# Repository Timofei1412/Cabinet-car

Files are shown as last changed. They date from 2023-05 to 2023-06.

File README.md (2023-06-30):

# Команда Кабинетный Болид
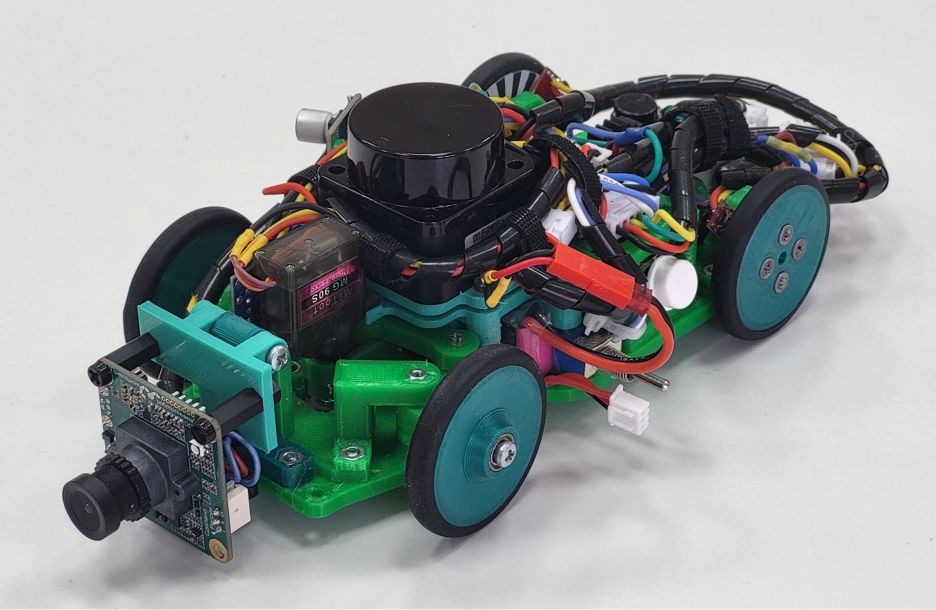
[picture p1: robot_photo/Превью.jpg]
General


### Робот, созданный для решения задачи РРО Будущие инженеры 2023
### © Беззубцев Федор, Федоров Тимофей 

## Наши фотографии
  [Обычная фотография](https://github.com/Timofei1412/Cabinet-car/blob/main/team_photo/Фотграфия%20команды.jpg)
  [Смешная фотография](https://github.com/Timofei1412/Cabinet-car/blob/main/team_photo/Смешная%20фотография.jpg)
<br>

## Видео заезда нашего робота на [Youtube](https://www.youtube.com/watch?v=HyZGGjBNKJ4&ab_channel=qZer0)
<br>

## Предисловие
  > Робот является автомобилем с передними поворотными колесами и задним приводом. На роботе установлены: лидар, для определения стенок и кубиков, на подпружиненной основе (для более удобной настройки уровня лидара), камерой для определения цвета кубиков и энкодер на ведущем двигателе, для определения пройденного расстояния. Система курсового управления автомобиля управляется сервомотором. При проектировании были учитаны углы Аккермана и принцип трапеции Жанто. Во главе робота находится микроконтроллер ESP32.
  
## Содержание репозитория
  - Папка "Robot models" содержит все модели старой версии робота
  - Папка "Code" содержит код робота
  - Папка "schematic" содержит электромеханическую схему робота
  - Папка "team_photo" содержит два фото команды по регламенту
  - Папка "robot_photo" содержит обзорные фото робота с шести сторон
  - Папка "readme_photo" содержит фото, используемые в README.md файле

## Фото робота
  Здесь представлены фото робота спереди, сзади, справа, слева, сверху и снизу.
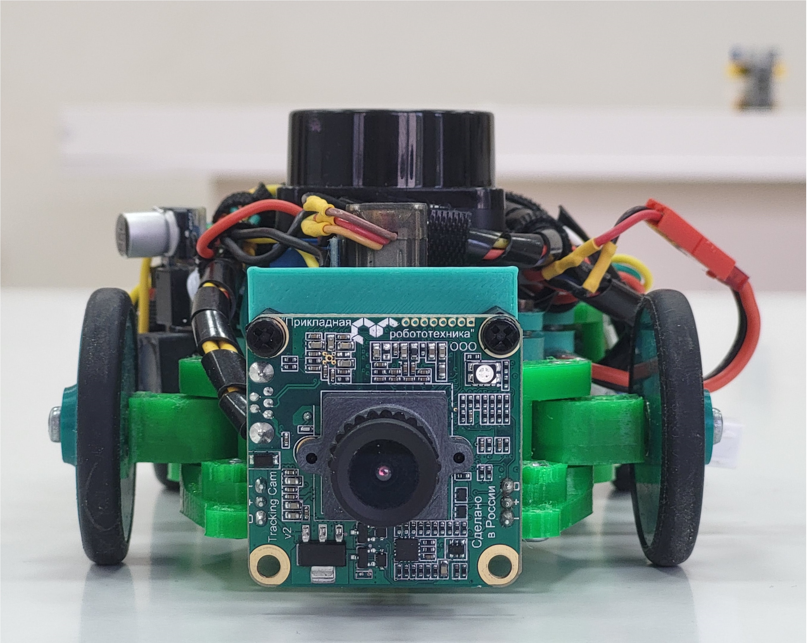
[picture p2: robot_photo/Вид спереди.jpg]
Front
  
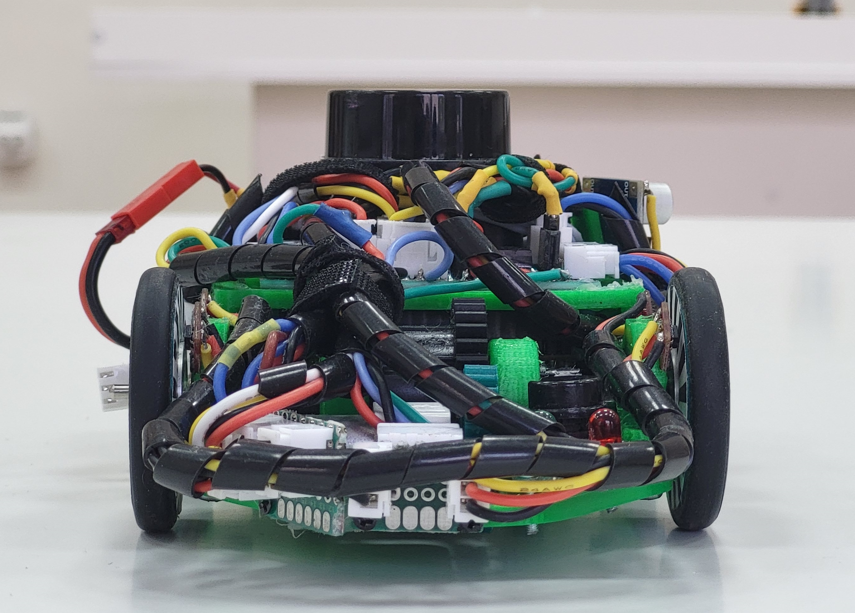
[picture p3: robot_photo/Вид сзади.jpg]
Back
  
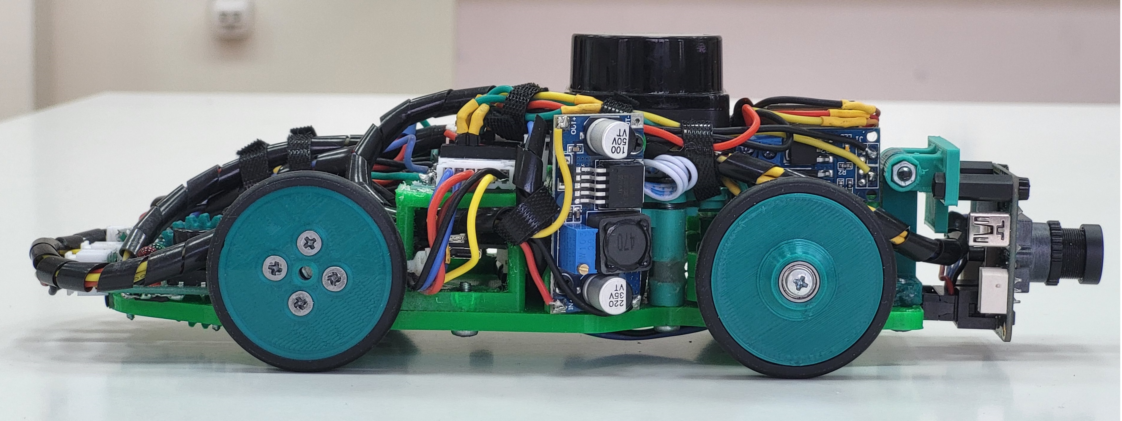
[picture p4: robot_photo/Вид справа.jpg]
Right
  
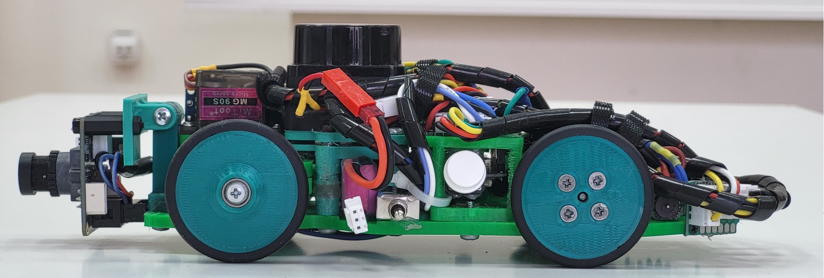
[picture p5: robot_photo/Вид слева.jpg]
Left
  
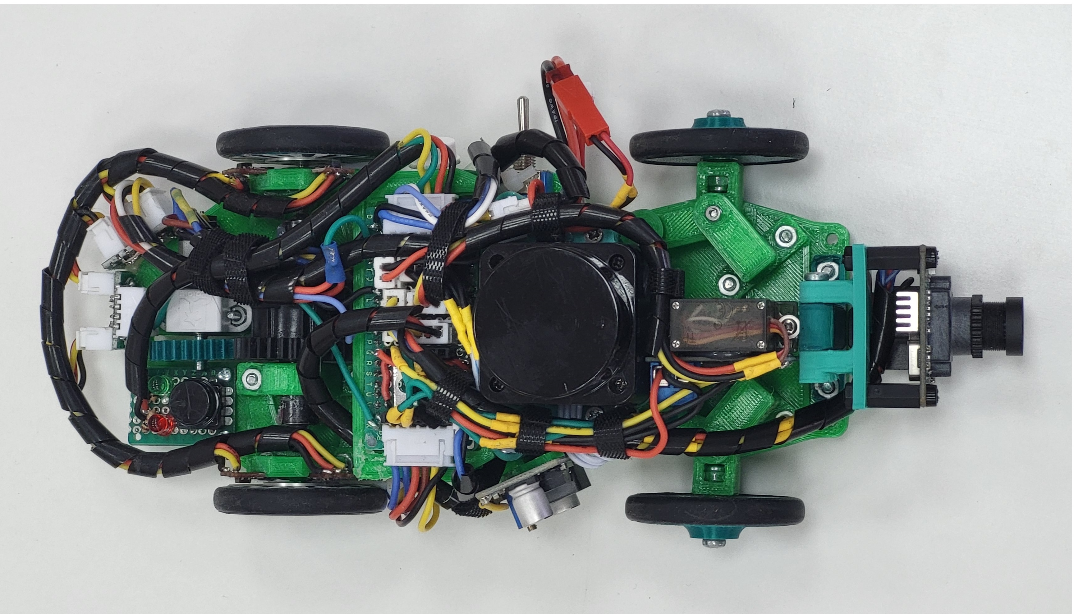
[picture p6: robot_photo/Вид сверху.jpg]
Top
  
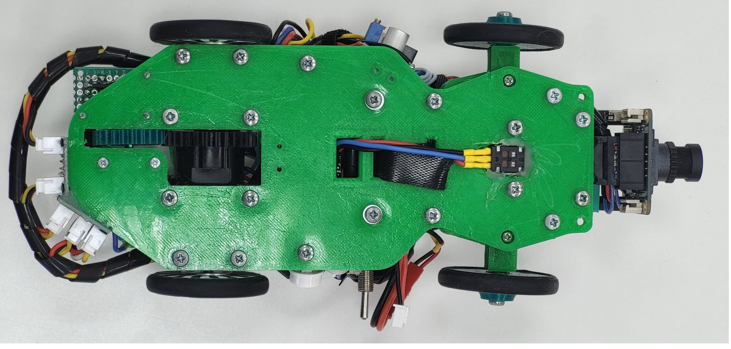
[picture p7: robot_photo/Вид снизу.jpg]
Bottom
  
  
  *Если картинки не открываются, проверьте папку "robot_photo", пожалуйста
  
## Подсистема перемещения робота
  Система перемещения робота была полностью спроектированна и собранна участниками команды. Робот использует детали, напечатанные на 3D принтере. Для соединений деталей используются винты и гайки М2 и М3. В креплении дифференциала и в рулевом управлении использованы подшипники и латунные втулки, уменьшающие трение.
  
  Для движения робота вперёд используется коллекторный двигатель Polulu с редуктором. Задние колёса соеденены с мотором при помощи дифференциала, который позволяет роботу правильно проходить повороты. Дифференциал закреплён к корпусу робота. Для контроля направления движения робота используется сервомотор MG90S с металлическим редуктором, а также система тяг и кулаков. Сервомотор вращает качалку, которая в свою очередь тянет тяги, которые врашают кулаки на которых закреплены передние колёса колёса. Для связи тяг и кулаков используется система из запресованных в пластик подшипников, подшипники соеденены между собой винтом. При расчёте системы рулевого управления использовались углы Аккермана.
### Фотографии системы рулевого управления
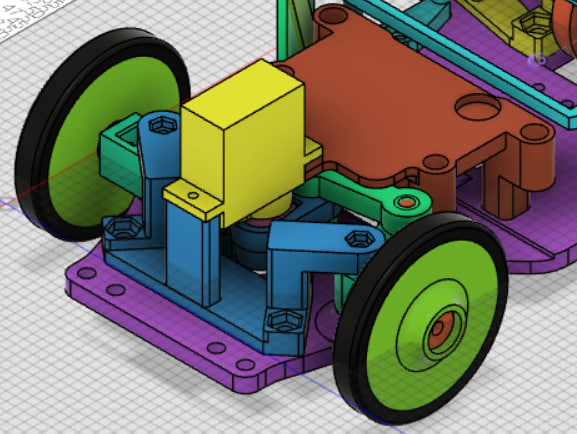
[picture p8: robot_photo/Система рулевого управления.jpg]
Система
  

## О наших электрических и механических компонентах
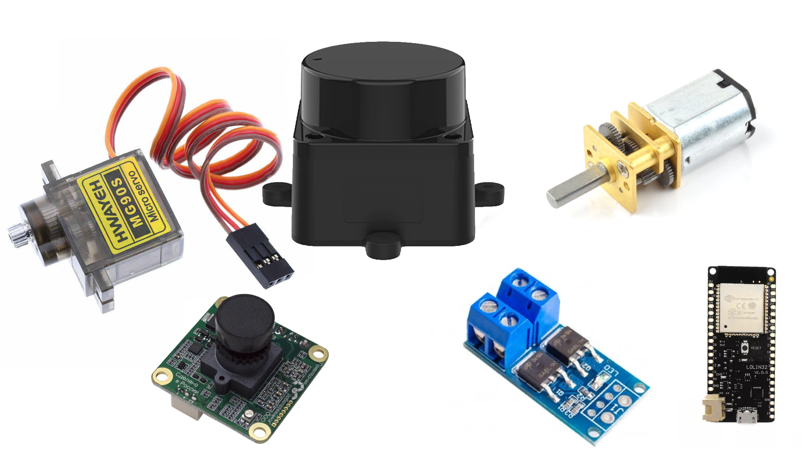
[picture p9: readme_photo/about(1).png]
About

### Лидар
  В нашем роботе используется LD19. Он основан на принципе лазерной триангуляции расстояния и использует высокоскоростной процессор для сбора и обработки данных. Система измеряет данные о расстоянии более 4500 раз в секунду. Дальномер LD19 вращается по часовой стрелке и выполняет 360-градусное лазерное сканирование окружающего пространства. Полученные данные преобразуются главным микроконтроллером для построения виртуальных стен. Данный лидар имелся в наличии и является достаточно простым для использования, поэтому мы решили использовать именно его.

### Камера
  Для определения цвета знаков было решено использовать модуль технического зрения TrackingCam. Он является сенсорным устройством для исследования окружающего пространства путем обработки и анализа изображения со встроенной видеокамеры. Данная камера проста в настройке и использовании.

### Драйвер двигателя
   В качестве драйвера двигателя используется модуль MOSFET транзистора D4184. Данный модуль неприхотлив, прост в использовании. Однако у данного модуля есть один существенный минус: двигатель, под управлением данного драйвера, не имеет возможности двигаться в обратном направлении.

### Металлический мотор-редуктор Polulu
  Этот мотор-редуктор представляет собой миниатюрный двигатель постоянного тока средней мощности с обмоткой на 6 В и металлическим редуктором. Его поперечное сечение составляет 10 × 12 мм, а D-образный выходной вал редуктора имеет длину 9 мм и диаметр 3 мм.
  Эти миниатюрные щеточные моторы-редукторы постоянного тока выпускаются в широком диапазоне передаточных чисел - от 5:1 до 1000:1 - и с пятью различными двигателями: мощными 6 В и 12 В с угольными щетками с длительным сроком службы (HPCB), а также двигателями высокой (HP), средней (MP) и малой (LP) мощности 6 В с щетками из драгоценных металлов с меньшим сроком службы. Двигатели HPCB на 6 В и 12 В обладают одинаковой производительностью при соответствующих номинальных напряжениях, только двигатель на 12 В потребляет вдвое меньше тока, чем двигатель на 6 В. В нашем роботе используется двигатель 50:1 HPCB на 6 В.
  
### Магнитный энкодер Polulu
  На роботе команды "Кабинетный болид" закреплён магнитный энкодер polulu. На валу мотора закреплён диск магнитная полярность которого различна в разных точках. Энкодер сосоит из двух датчиков хола смещённых на 90 градусов друг относительно друга. Мы получаем с энкодера два сигнала смены магнитной полярности смещённые на 90 градусов. Это позволяет точно определить скорость вращения мотора и поддерживать её постоянной на протежение всего заезда. Данный энкодер был специально спроектирован для линейки двигателей polulu и использовать другой(сторонний) энкодер было не целесообразно 

### Датчик линии QTR-01A
  На роботе установлены четыре датчика линии QTR-01A. На основе данных датчиков мы создали свои кастомные энкодеры на ведущие колеса. Таким образом мы собираемся коректировать ошибку лидара при движении робота.

### Потенциометр
  Потенциометр на нашем роботе встроен в дно и в будующем поможет(всесте с энкодерами на задних ведущих колесах) более точно корректировать показания лидара.
### Сервопривод MG90S
  MG90S - это маленький сервопривод похожий на популярную версию MG90. Так почему бы не использовать его синий аналог? Ответ прост - металлический редуктор. Благодаря ему сервопривод может приложить большое усилие для поворота колес без каких-либо последствий. С помощью этого сервопривода робот может довольно точно задать угол поворота колес. 
### ESP32
  Плата Lolin D32 основана на микроконтроллере ESP32 от "Espressif systems" с низким энергопотреблением. Она обладает множеством мощных функций, включая двухъядерный процессор на базе Arm, Wi-Fi, Bluetooth, I2C, I2S, SPI, АЦП, ЦАП и 4 Мб флэш-памяти. Модуль D32 предоставляет эти функции в удобном формате DIP и может быть запрограммирован непосредственно с USB-интерфейса - дополнительное оборудование для программирования не требуется.

## Подсистема питания и сенсоры робота 

### Питание
  Источником питания робота является литий-полимерная батарея с номинальным напряжением 8.7 вольта. Для полного отключения питания робота, на плате размещен тумблер. На плате установлен делитель напряжения который позволяет контроллеру безопасно считать текущее напряжение акумулятора и предотвратить его разряд. На плате напряжение с акумулятора понижается до 5в при помощи схемы на основе модуля [MP1584](https://www.ozon.ru/product/ponizhayushchiy-preobrazovatel-napryazheniya-gsmin-mp1584en-dc-dc-zelenyy-285604865/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) для подачи его на лидар серву и камеру, ESP32. Для подачи на драйвер двигателя напряжение с акумулятора повышается до 8в при помощи схемы на основе модуля [LM2577](https://ampero.ru/lm2577-voltage-regulator-povyshayuschiy-dc-dc-preobrazovatel-3v-34v-v-4v-35v.html). 
  
### Сенсоры
  Основным сенсором для определения стенок и кубиков является лидар, он позволяет узнавать расстояние до 300 точек вокруг робота с частотой обновления 15 раз в секунду. Поскольку лидар не имет возможности чётко определять цвет объекта перед роботом, для этой цели используется камера TrackingCam.

## Схема электромеханического устройства
  В этом блоке представлена схема основной печатной платы робота. Файл схемы печатной платы можно найти [в этой папке](https://github.com/Timofei1412/Cabinet-car/blob/main/schematic).
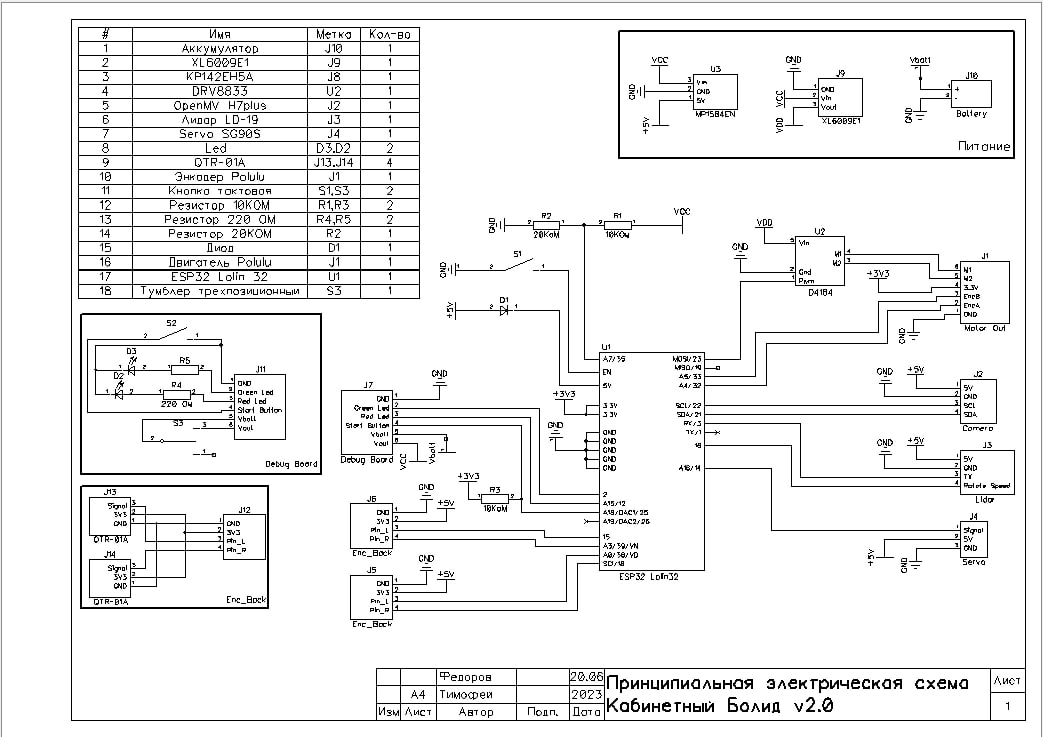
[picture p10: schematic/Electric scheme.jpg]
Общая схема
  
  
  *Если картинка не открывается или вам нужна картинка лучшего качества, проверьте папку "schematic", пожалуйста.

## Сборка робота
  1) Необходимо напечатать все пластиковые части на 3D принтере. Для этого зайдите в папку "3D-models" и распечатайте все модели на 3D-принтере.
  2) Необходимо купить такие компоненты как: [Esp32 Lolin32](https://compacttool.ru/plata-razrabotchika-wemos-lolin32-esp-wroom-32-bluetooth-btblewifi), [Понижающий преобразователь](https://www.ozon.ru/product/ponizhayushchiy-preobrazovatel-napryazheniya-gsmin-mp1584en-dc-dc-zelenyy-285604865/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), [Повышающий преобразователь](https://ampero.ru/lm2577-voltage-regulator-povyshayuschiy-dc-dc-preobrazovatel-3v-34v-v-4v-35v.html), [лидар LD-19](https://aliexpress.ru/item/1005004295339153.html?sku_id=12000031808972433), [камеру TrackingCam](https://robotbaza.ru/product/modul-tehnicheskogo-zreniya-trackingcam), [мотор Polulu](https://www.pololu.com/product/3063), [сервопривод SG-90S](https://ampero.ru/mg90s-servoprivod-dlya-proektov-arduino.html), [драйвер мотора](https://www.wildberries.ru/catalog/60795780/detail.aspx). Для робота также необходимы 4 подшипника 3x9x7, 16 подшипников 2x5x2.5, 2 подшипника 10x15x6, латунные втулки 3x6x4, [дифференциал](https://rc-today.ru/product/differencial-hsp-60065/) и четыре силиконовые [шины Pololu](https://www.pololu.com/product/3408). Для питания робота можно использовать любую 7.4V 2S Li-Po батарею размером 53x30x11.5мм, например, мы используем вот эту [батарею](http://realrc.ru/product.php?id_product=416).  
  3) Для сборки напечатаных и купленных компонентов понадобится 16 винтов и гаек различных размеров(М3 /16, /10... и М2 /10):
  4) В соответствии с файлом печатной платы, спаяйте печатную плату робота (папка "schematic").
  5) Открыв 3Д файл робота в [папке](https://github.com/Timofei1412/Cabinet-car/tree/main/Robot%20models/New%20robot%20models), соберите робота, как показано на модели.

## Распознование стенок и препядствий
  Для распознования стенок используется алгоритм апроксимации набора точек до прямой. Робот путём геометрических вычеслений, определяет расстояние до окружающих его стенок, и высчитывает свою координату относительно одного из углов поля. Движение робота (в первоначальном виде) осуществляется при помощи системы точек, по которым робот должен проехать. Основные точки ставятся програмно, при старте робота и находятся в начале и конце каждого прямого сегмента (по середине между стенками). По нахождению кубика робот ставит в соответствущей регламенту стороне две точки: сбоку перед и сбоку за кубиком. Для распознования кубиков робот смотрит есть ли какие либо точки в местах, где должны располагатся кубики, если такие точки есть, то кубик есть, а если нет, то кубика нет. Для определения цвета кубика используются данные с камеры. Для дополнительной информации откройте код.
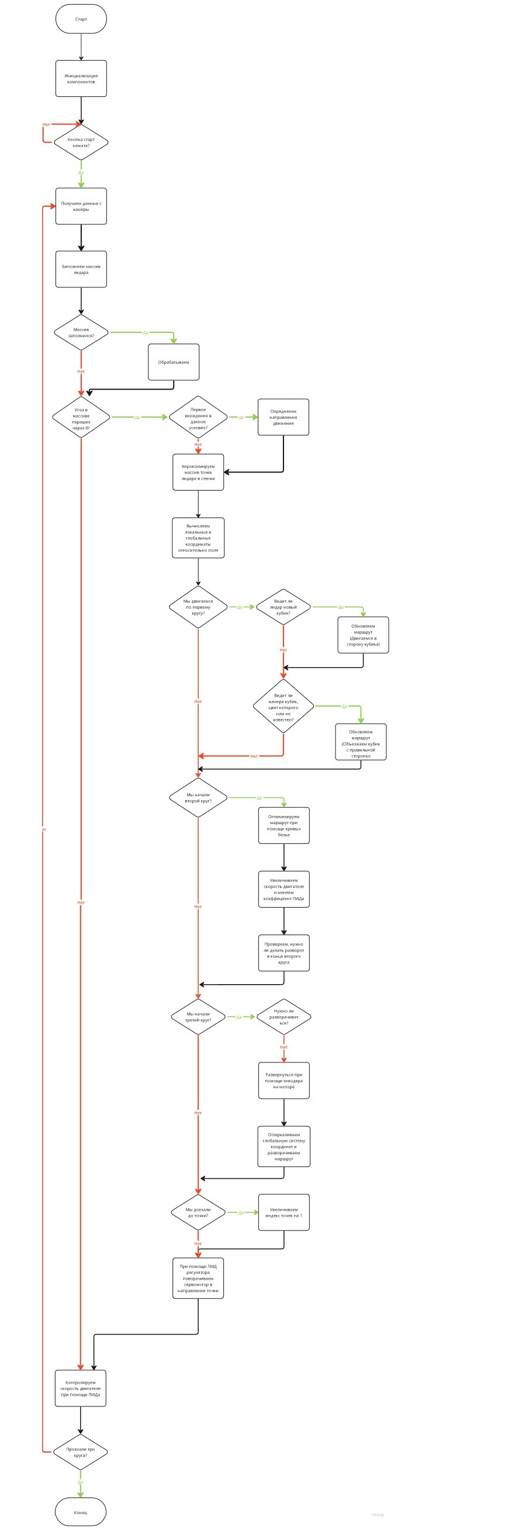
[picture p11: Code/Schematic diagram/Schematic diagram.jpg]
блоксхему
  
  
  *Если картинка не открывается или вам нужна картинка лучшего качества, проверьте папку "Schematic diagram", пожалуйста.
  
## Установка необходимых программ и прошивка платы

  - Для программирования робота вам понадобится [Arduino IDE](https://www.arduino.cc/en/software). Это программное обеспечение с открытым исходным кодом позволяет легко писать код и загружать его в плату. Откройте exe-файл и следуйте инструкциям программы установки.

  - Установите ESP32 в менеджере плат Arduino IDE, добавив ссылку (https://dl.espressif.com/dl/package_esp32_index.json) в настройки IDE.
    - Сначала добавьте дополнительные ссылки менеджера плат
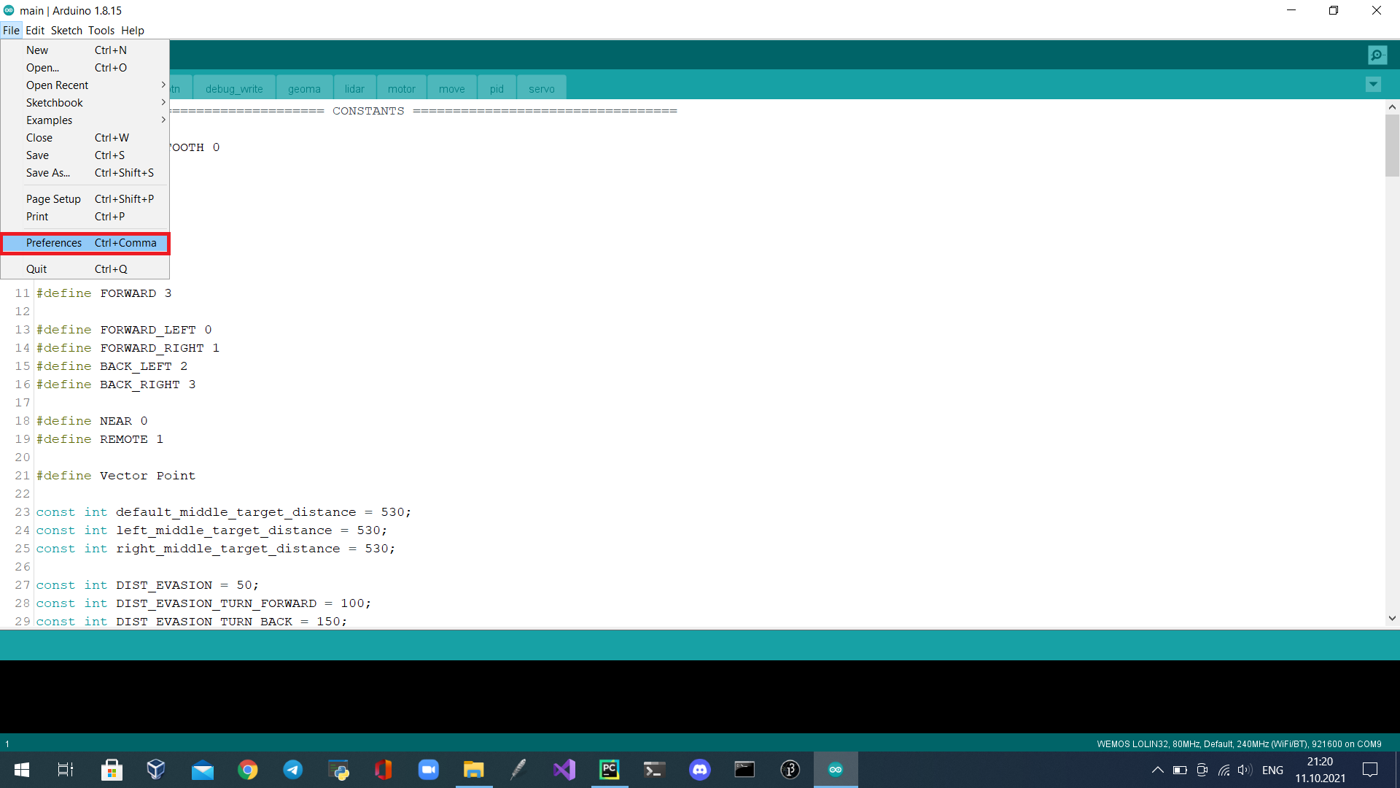
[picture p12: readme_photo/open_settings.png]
Settings
    
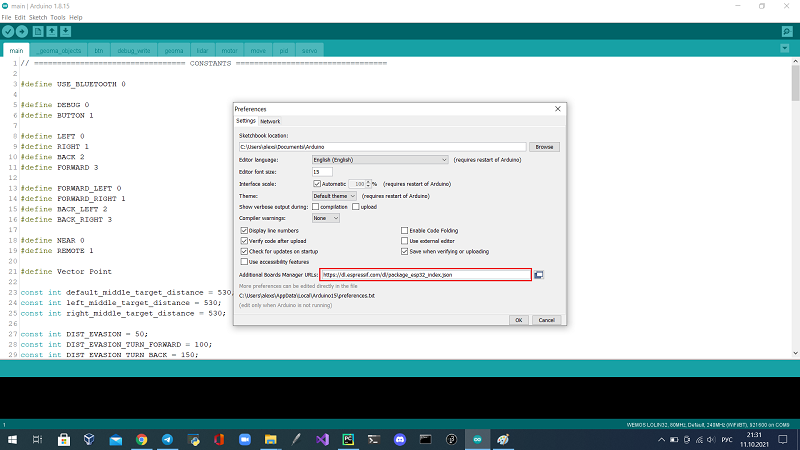
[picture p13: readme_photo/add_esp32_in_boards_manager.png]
Менеджер
    
    - Во-вторых, установите плату
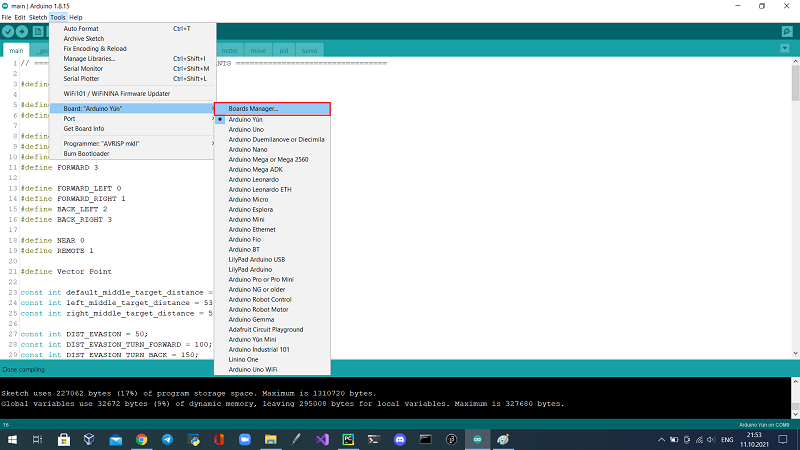
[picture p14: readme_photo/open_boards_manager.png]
Boards
    
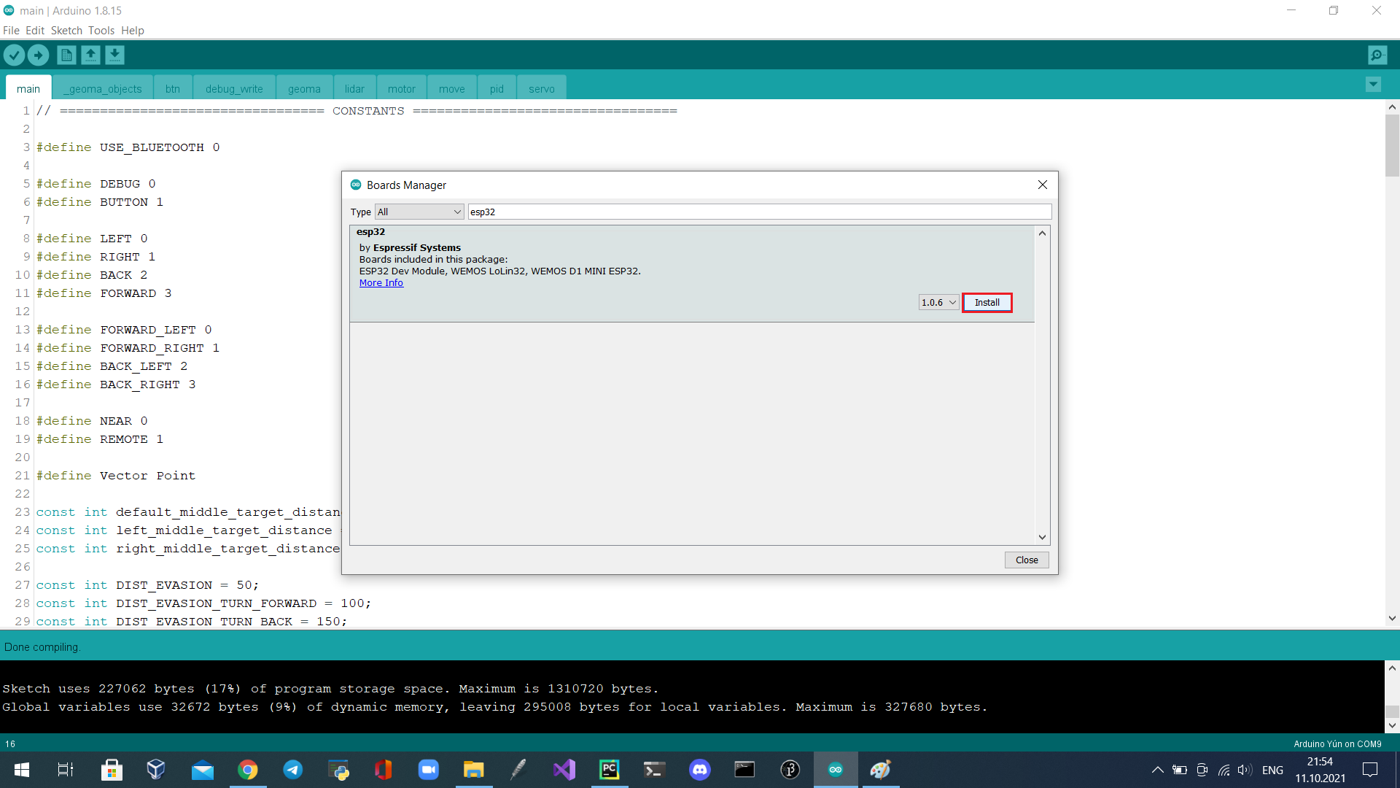
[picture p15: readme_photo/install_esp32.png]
Install
    
  - Используйте менеджер библиотек для установки библиотек ESP32.
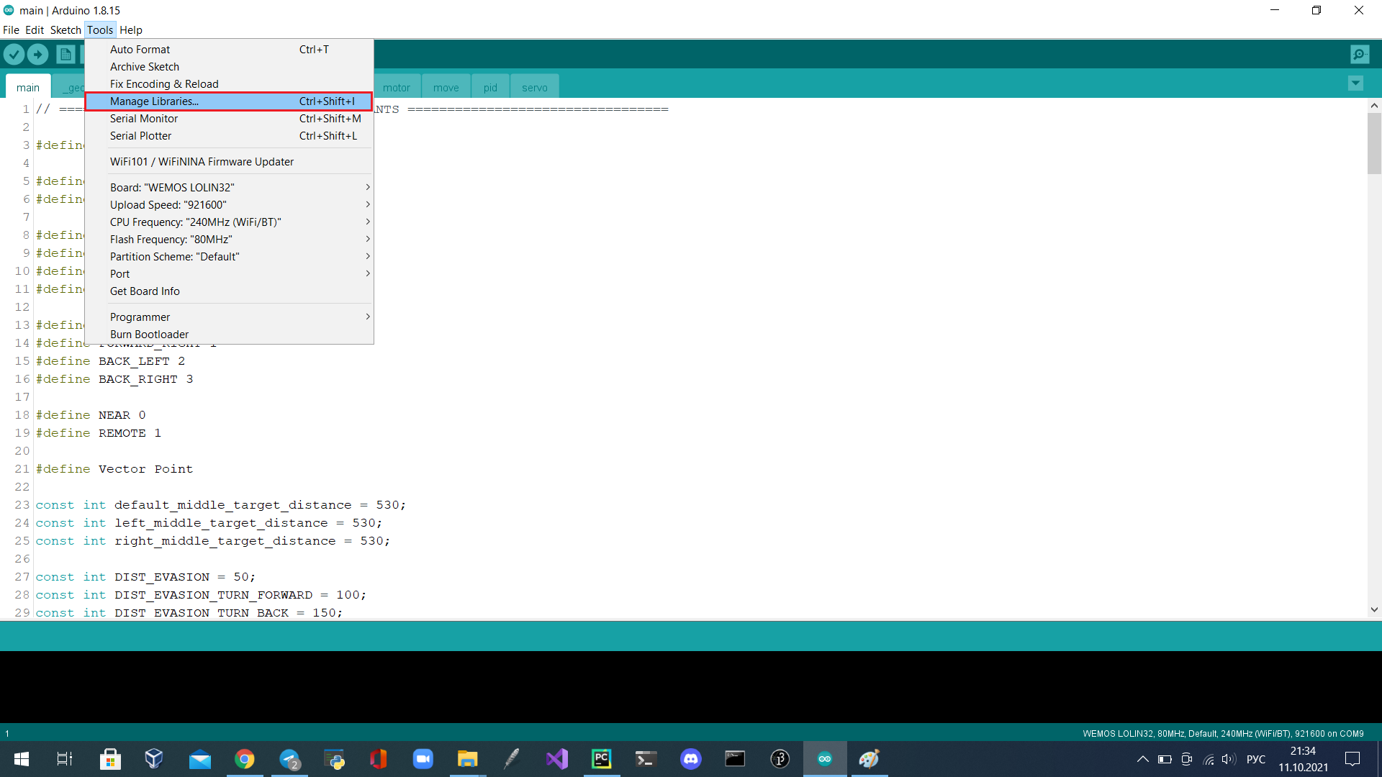
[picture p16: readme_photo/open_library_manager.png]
Открыть
  
    - Библиотеку для аналогового порта ESP32.
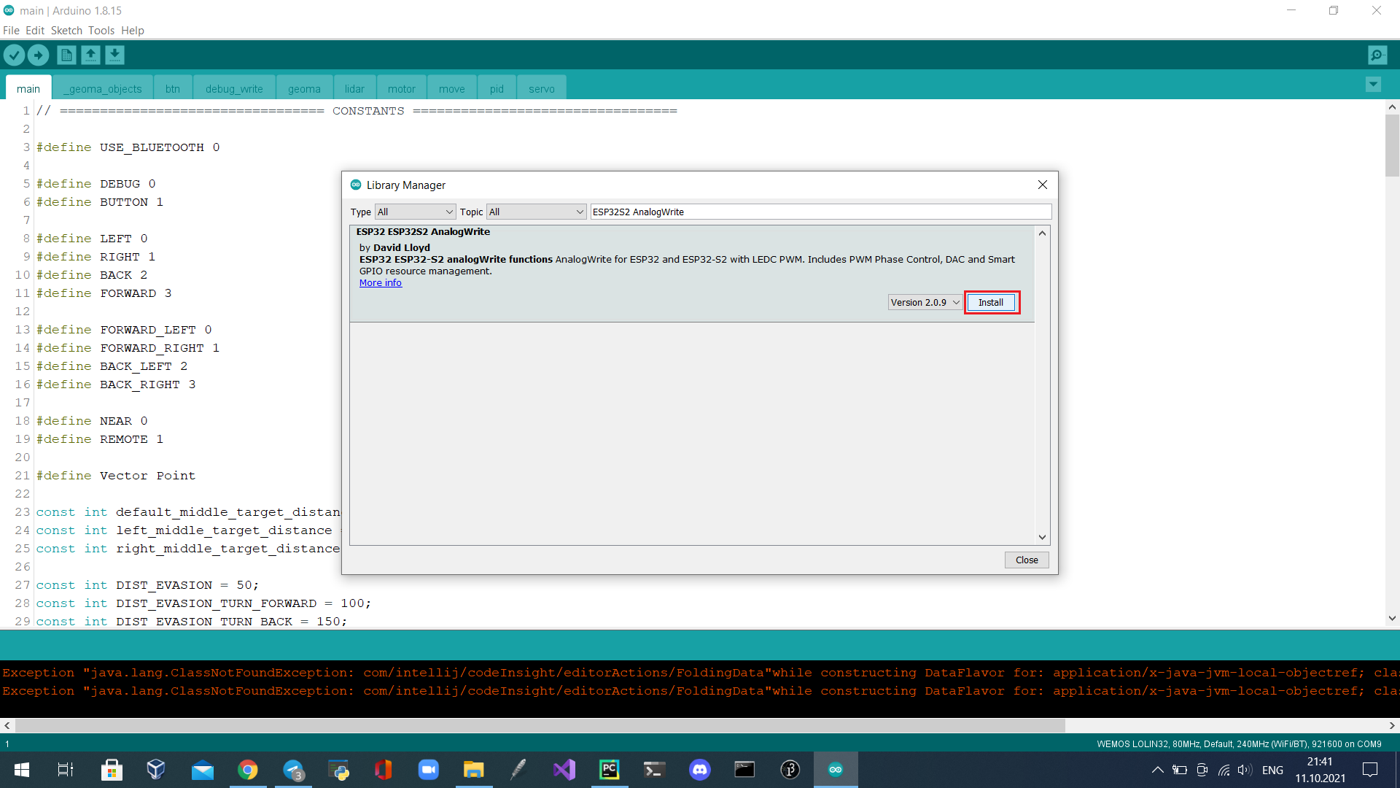
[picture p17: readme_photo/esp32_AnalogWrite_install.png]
AnalogWrite
    
    - И библиотеку ESP32Servo.
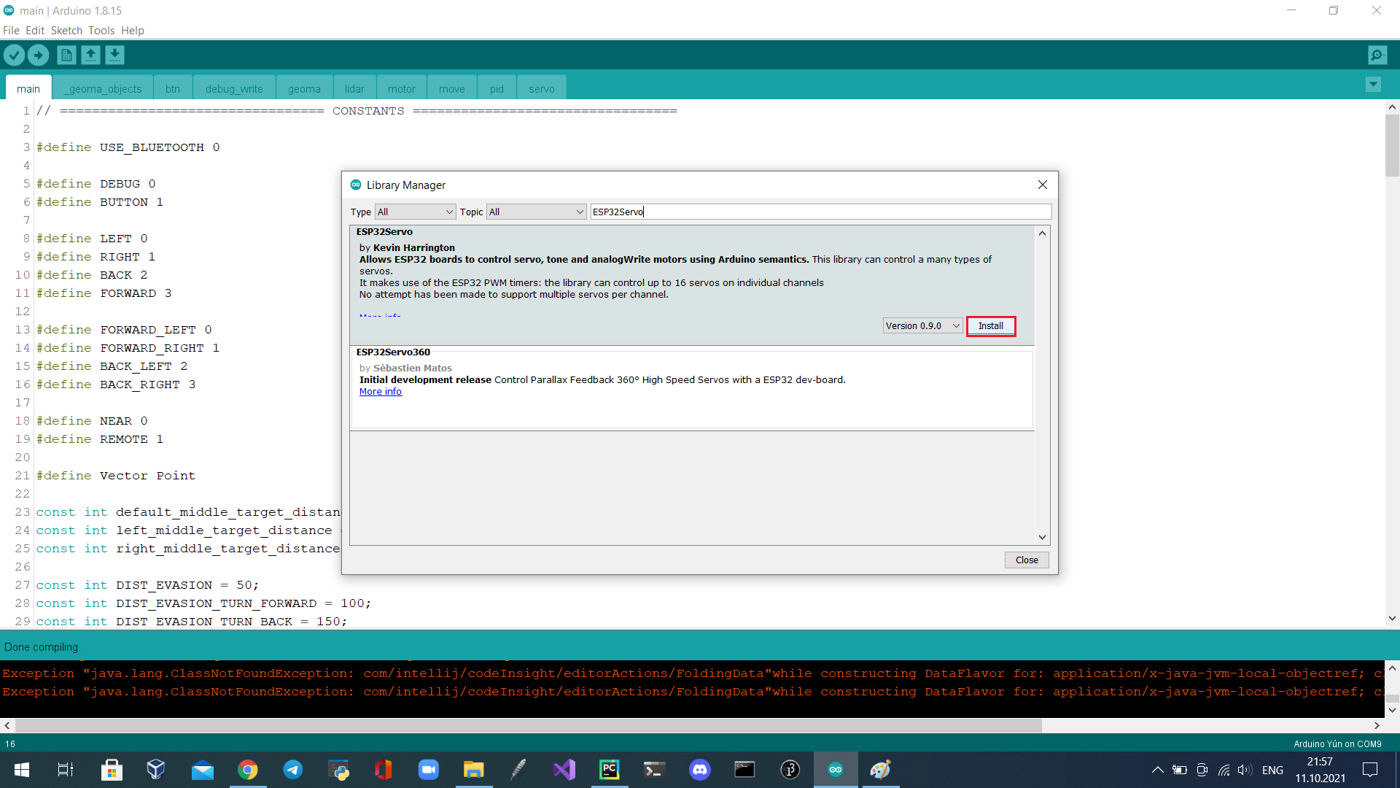
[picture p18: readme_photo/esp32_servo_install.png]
ESP32Servo
    
  - Выберите плату "WEMOS LOLIN32". Подключите плату с ESP32 с помощью кабеля Micro USB к компьютеру и выберите соответствующий порт в IDE arduino. Нажмите кнопку "Загрузить".
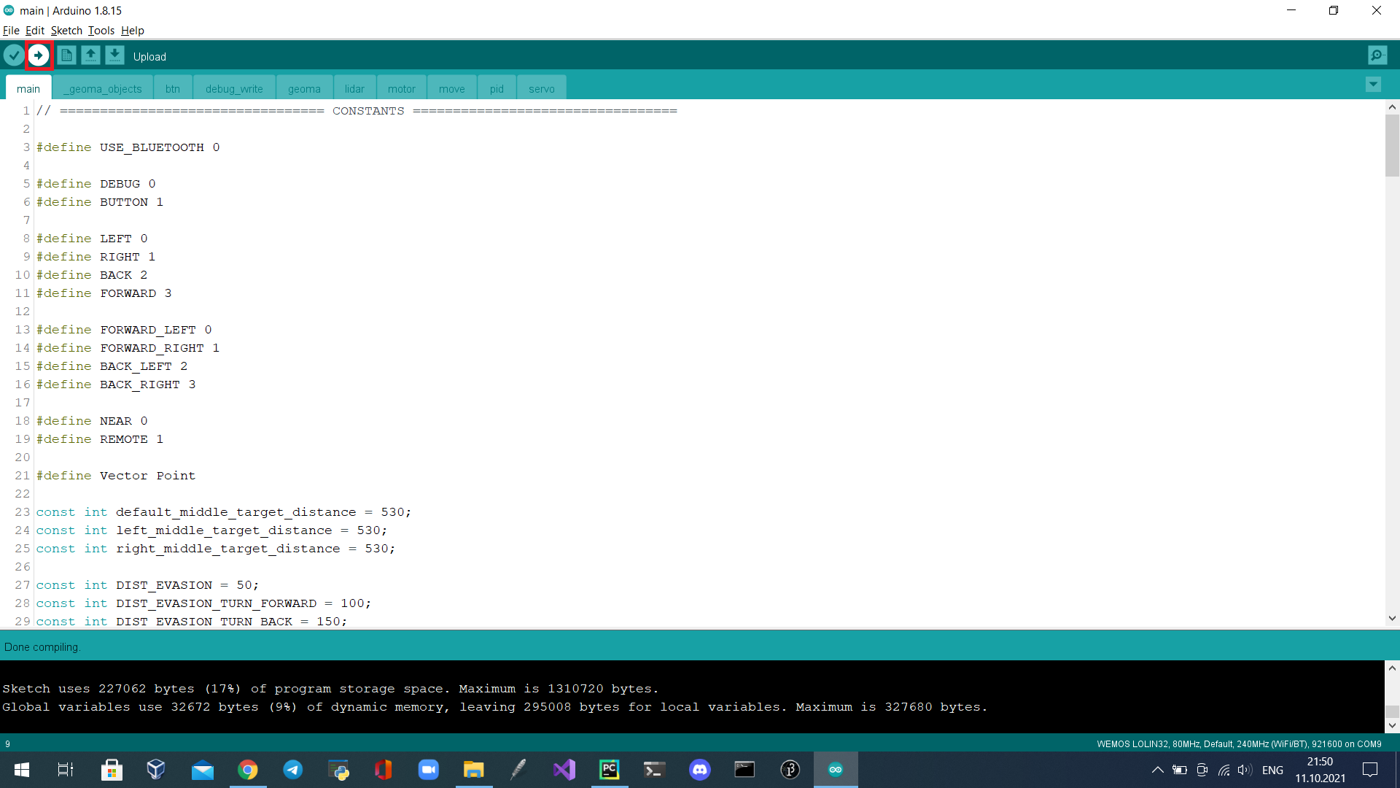
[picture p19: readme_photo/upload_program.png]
Upload
  
  
  - Также вам понадобится[TrackingCam](https://appliedrobotics.ru/?page_id=633). Скачайте и откройте exe-файл и следуйте инструкциям программы установки.
  - После скачивания откройте программу и настройте камеру.
    - Подключите камеру к компьютеру и откройте программу.
    - Подберите настройки для зеленого и красного кубика(не забудьте переключить поиск(полоска снизу)на блоб два, после настройки первого кубика, иначе настройки запишутся поверх прошлых)
    - Или поставьте их как на скриншоте:
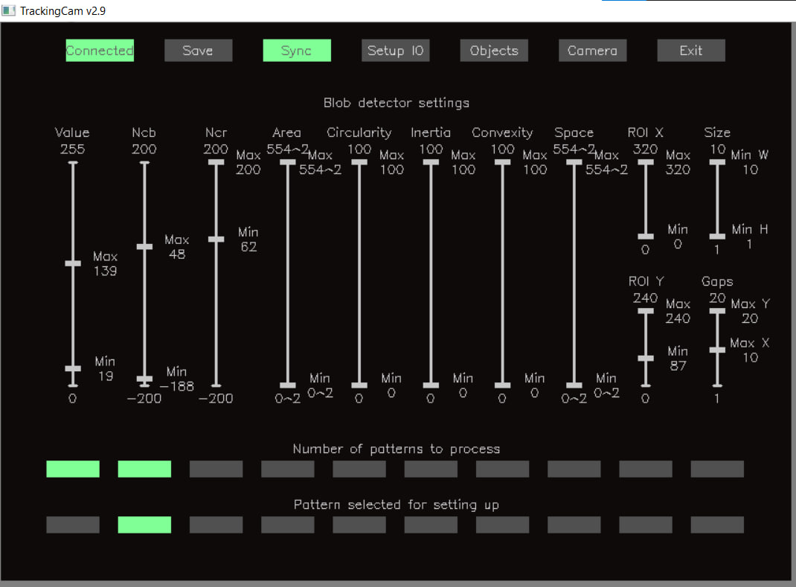
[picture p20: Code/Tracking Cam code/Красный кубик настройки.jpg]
Red
      
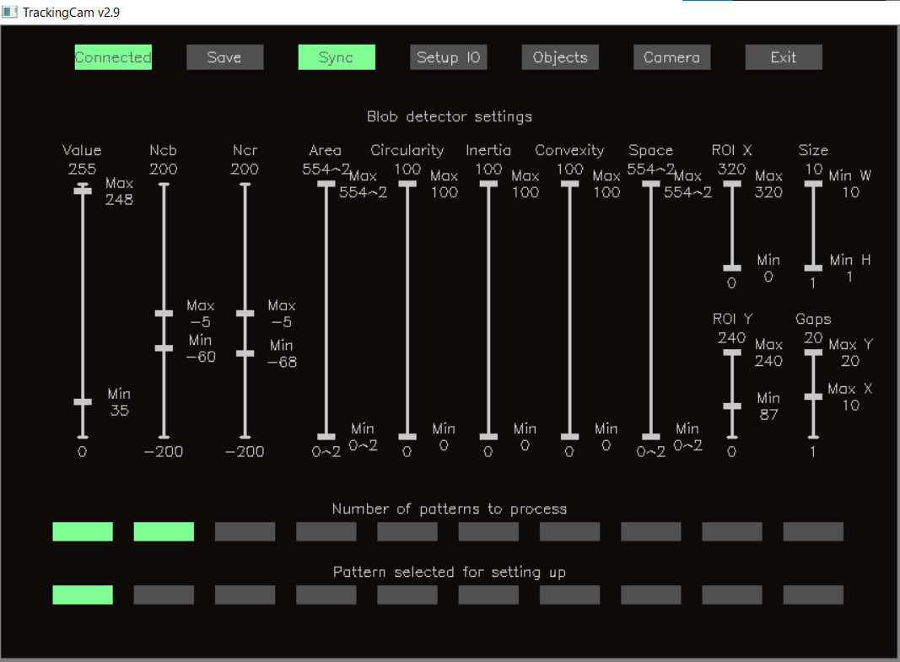
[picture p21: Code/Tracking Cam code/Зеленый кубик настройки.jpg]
Green
      
   * Настройки зависят от освещения и материала кубика. Те настройки, что указанны на скриншотах, могут не работать в вашем случае.

## Запуск робота
 - Загрузить в робота нужный код
 - Проведите жеребьевку, как указано в правилах
 - Поставьте робота на стартувую позицию
 - Включите робота переключением тумблера в замкнутое положение
 - Нажмите кнопку для запуска

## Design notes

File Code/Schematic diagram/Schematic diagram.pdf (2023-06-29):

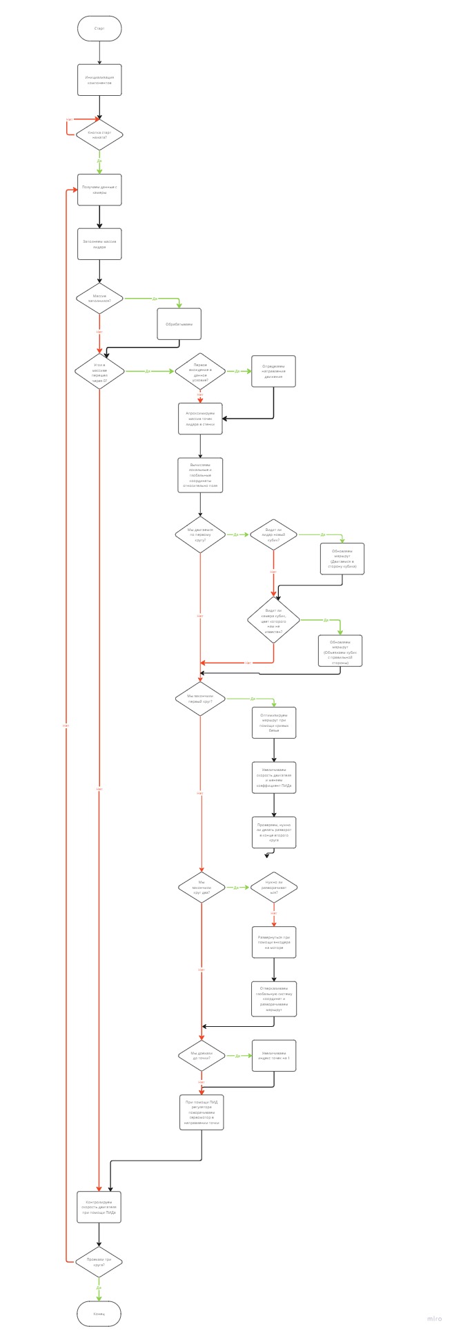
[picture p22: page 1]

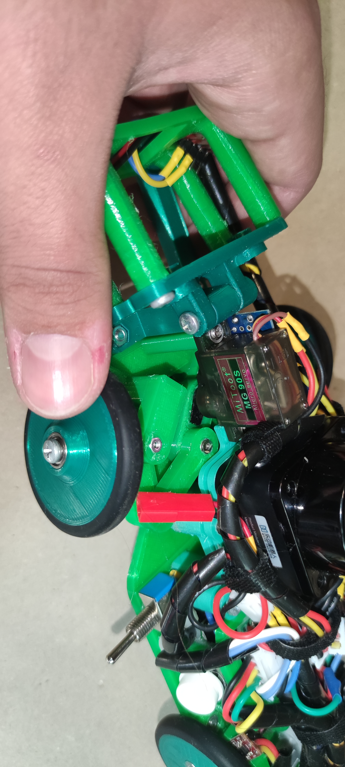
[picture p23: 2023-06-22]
robot_photo/Система рулевого управления робота.jpg

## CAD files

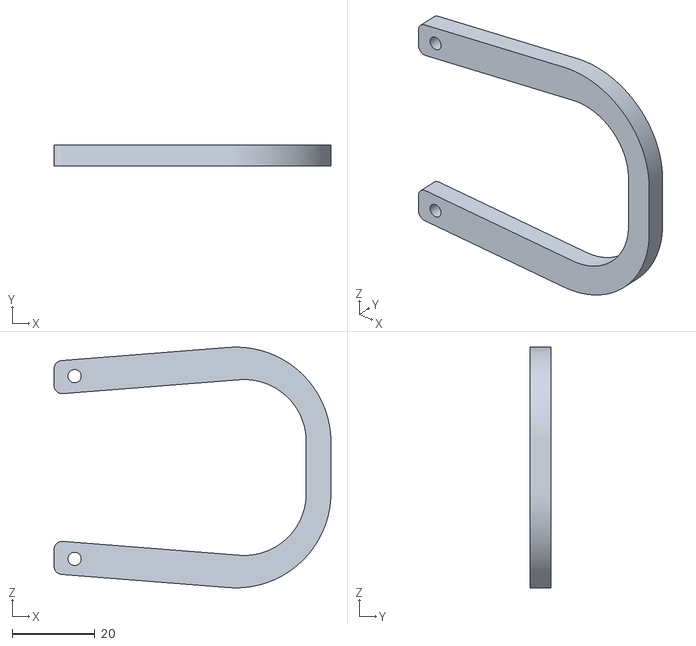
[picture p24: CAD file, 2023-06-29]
Robot models/New robot models/Защита от кубиков.stl
67.0 x 5.00 x 58.2

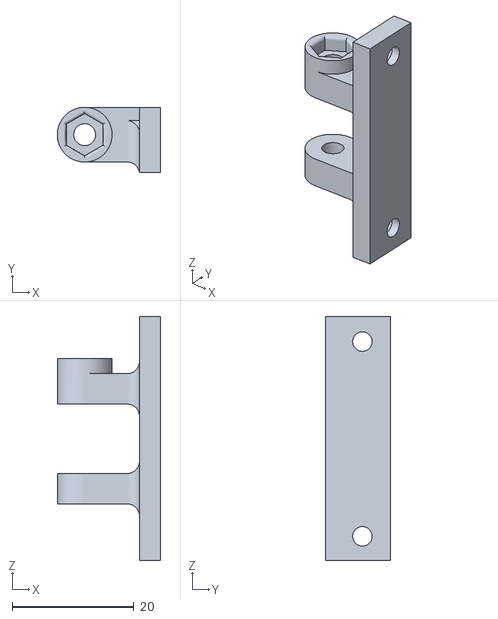
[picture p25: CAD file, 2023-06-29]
Robot models/New robot models/Платформа камеры.stl
17.0 x 10.8 x 40.1

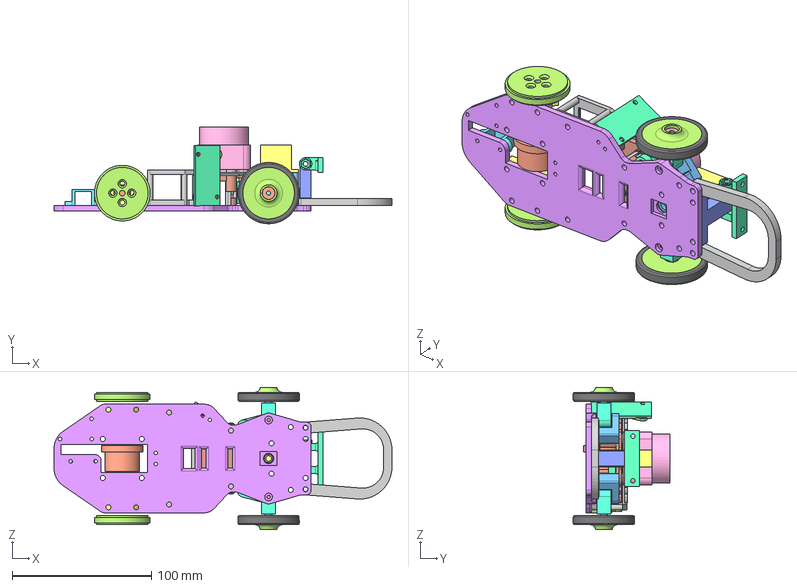
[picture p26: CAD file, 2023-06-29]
Robot models/New robot models/WRO v26.step
242.5 x 69.3 x 102.0 mm
Servo
Right x 2
Left x 2
Rear_wheel
Servo_rocker
Steering_fist_right
Steering_fist_left
Steering_rod_right
Steering_rod_left
Steering_fist_mount
Lidar
Lidar_holder
Rear_shaft_mount
Right_rod
Right_fist
Left_rod
Left_fist
Central
Differential
Motor_holder
Camera_mount_lower
Camera_mount_top
Base_detail
DC-DC_step_up
Step_up_holder
PCB V2
Lidar_holder_v2

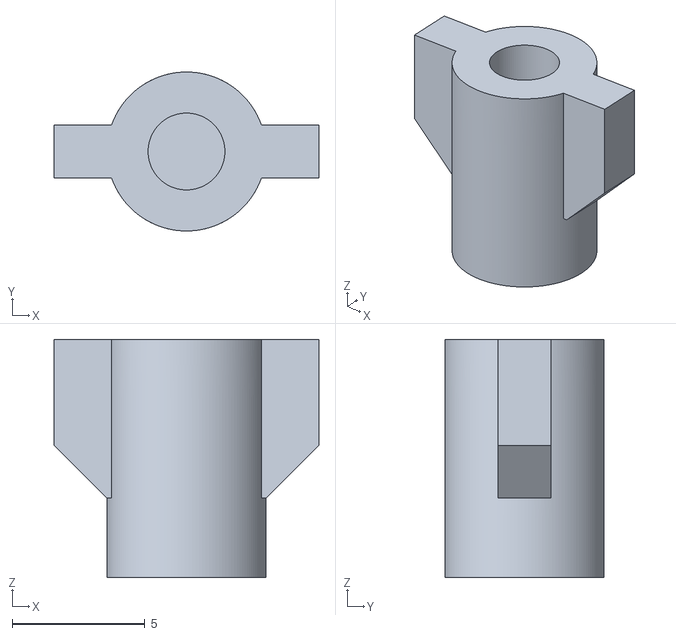
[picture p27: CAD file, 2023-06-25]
Robot models/New robot models/Втулка для дифференциала.stl
10.0 x 6.00 x 9.00

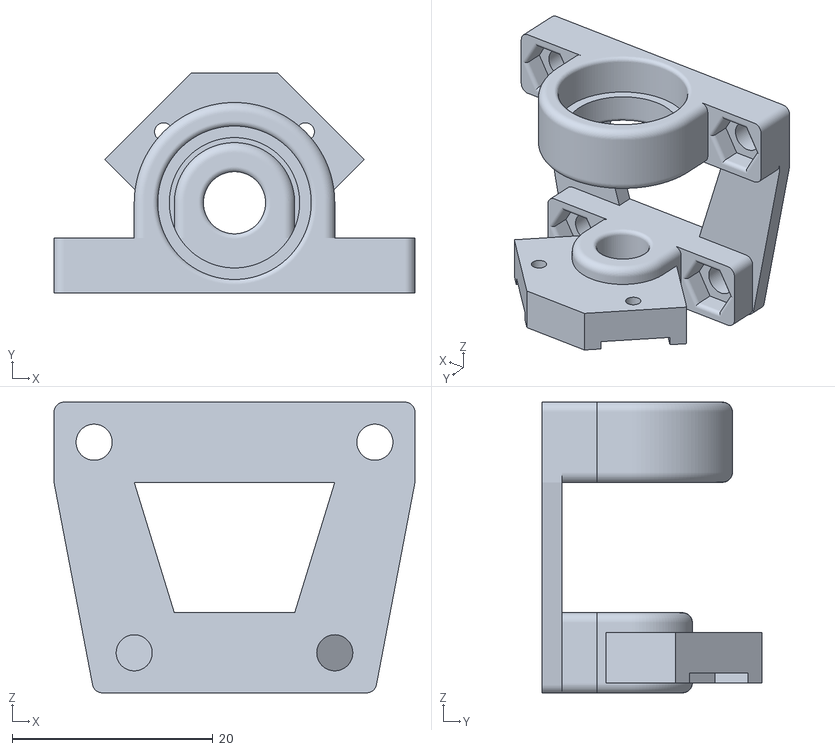
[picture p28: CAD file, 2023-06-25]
Robot models/New robot models/Держатель дифференциала левый.stl
36.0 x 21.9 x 29.0

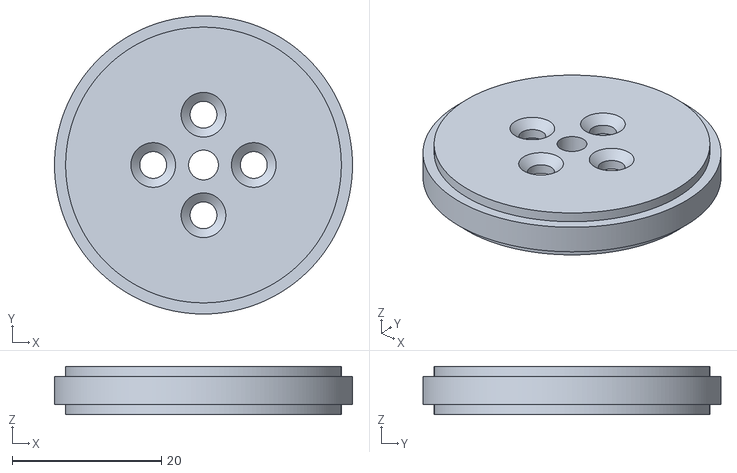
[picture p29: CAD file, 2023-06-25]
Robot models/New robot models/Диск задний правый.stl
40.0 x 40.0 x 6.50

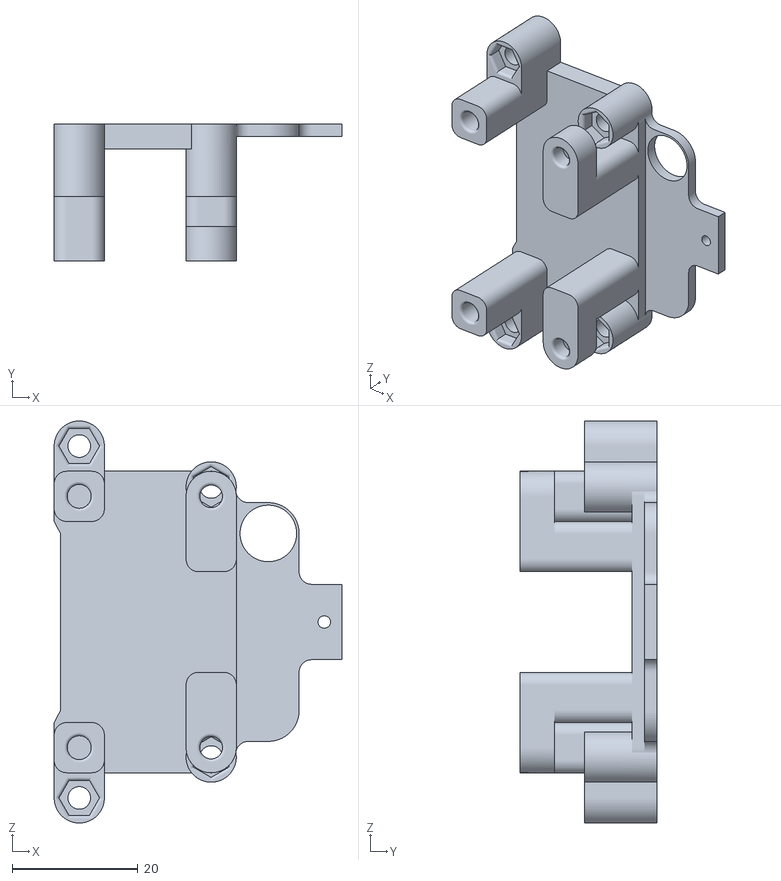
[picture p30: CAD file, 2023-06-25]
Robot models/New robot models/Нижняя платформа для лидара.stl
45.8 x 21.8 x 64.0

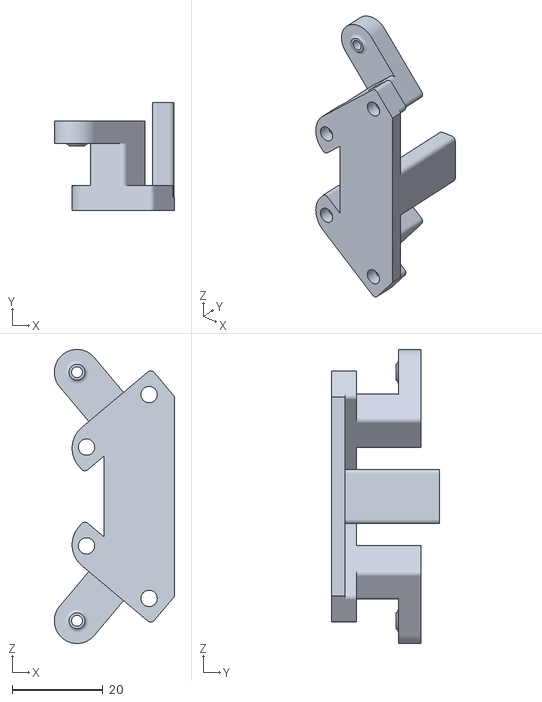
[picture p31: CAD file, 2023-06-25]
Robot models/New robot models/Держатель кулаков.stl
26.5 x 23.8 x 64.8

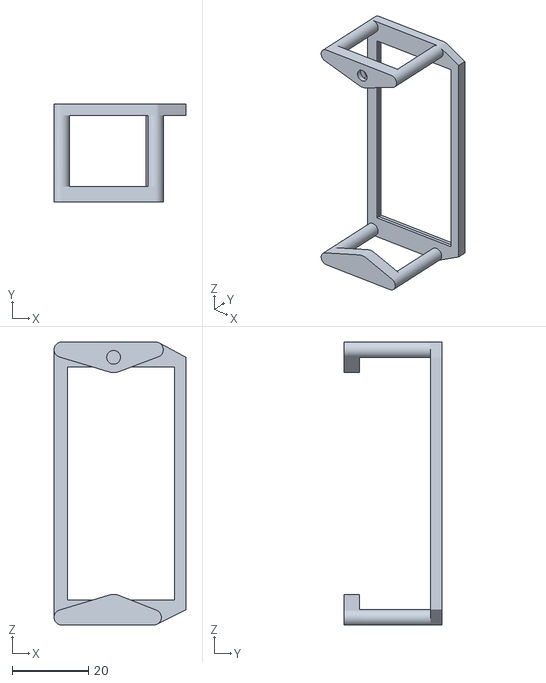
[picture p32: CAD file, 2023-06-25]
Robot models/New robot models/Кронштеин для платы.stl
34.5 x 25.5 x 74.0

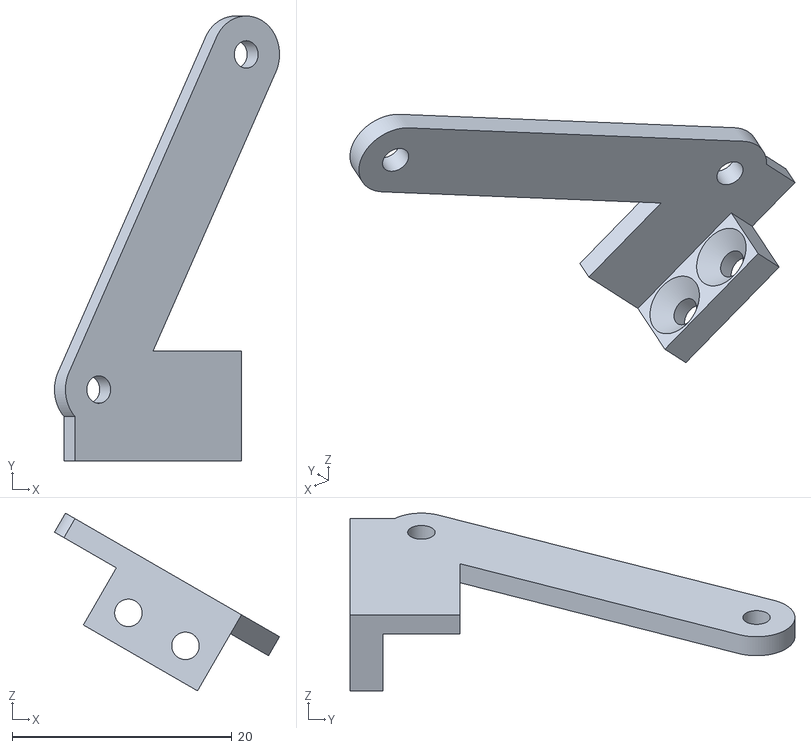
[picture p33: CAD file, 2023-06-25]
Robot models/New robot models/Держатель повышающего преобразователя.stl
20.5 x 40.5 x 16.2

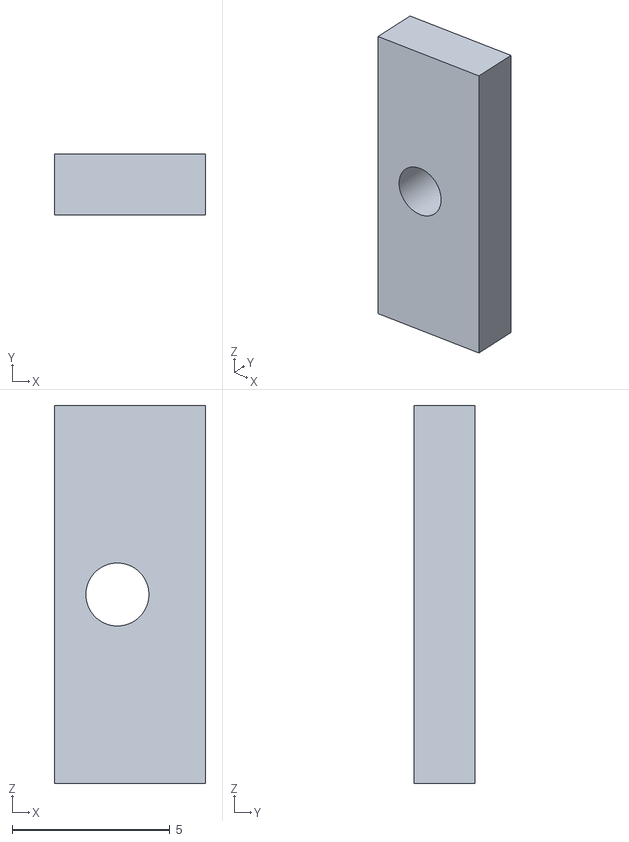
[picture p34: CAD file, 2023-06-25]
Robot models/New robot models/Проставка для сервомотора.stl
4.80 x 1.95 x 12.0

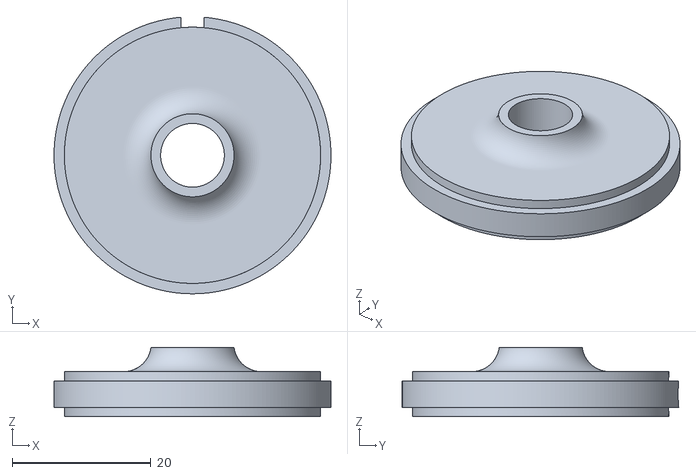
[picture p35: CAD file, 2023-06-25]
Robot models/New robot models/Диск передний правый.stl
40.0 x 39.9 x 10.0

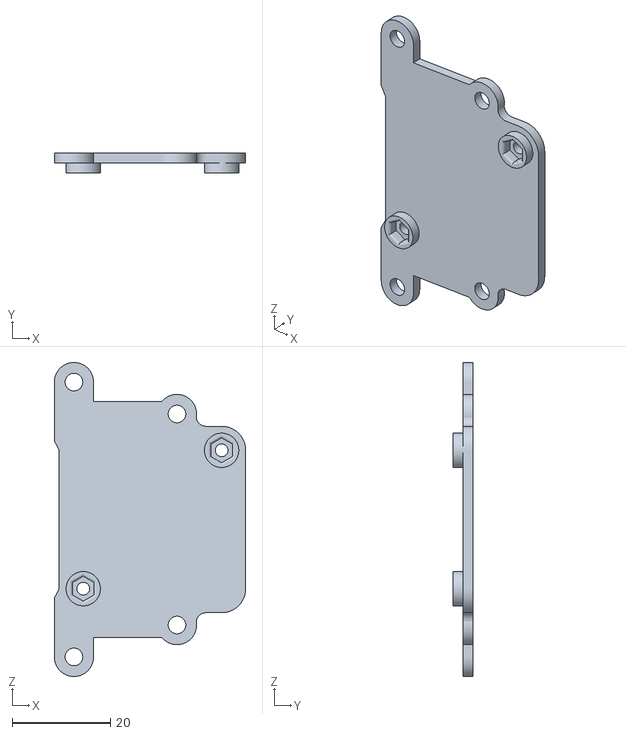
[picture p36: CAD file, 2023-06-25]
Robot models/New robot models/Верхняя платформа для лидара.stl
39.0 x 4.00 x 64.0

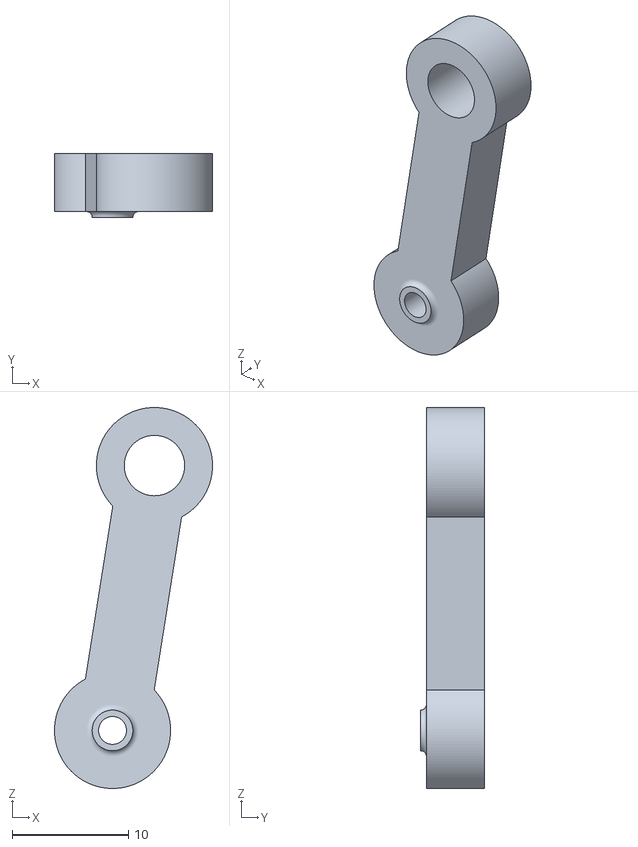
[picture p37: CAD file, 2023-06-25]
Robot models/New robot models/Тяга левая.stl
13.6 x 5.50 x 32.8

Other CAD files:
Robot models/New robot models/Диск задний левый.stl
Robot models/New robot models/Основа робота.stl
Robot models/New robot models/Поворотный кулак левый.stl
Robot models/New robot models/Качалка сервомотора.stl
Robot models/New robot models/Держатель дифференциала правый.stl
Robot models/New robot models/Диск передний левый.stl
Robot models/New robot models/Крепление камеры.stl
Robot models/New robot models/Поворотный кулак правый.stl
Robot models/New robot models/Тяга правая.stl
Robot models/Old robot models/Заднее колесо.stl
Robot models/Old robot models/Качалка сервы.stl
Robot models/Old robot models/Крепление вала заднего колеса.stl
Robot models/Old robot models/Крепление дифференциала.stl
Robot models/Old robot models/Крепление камеры верхняя часть.stl
Robot models/Old robot models/Крепление камеры нижняя часть.stl
Robot models/Old robot models/Крепление камеры.stl
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

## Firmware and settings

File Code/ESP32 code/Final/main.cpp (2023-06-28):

#include <define.h>

void setup() {
  Serial.begin(500000);
  SerialLidar.setRxBufferSize(512);
  SerialLidar.begin(230400, SERIAL_8N1, 16, -1);
  trackingCam.init(51, 400000);
  debug.begin("Robot debug");

  pinMode(red_led, OUTPUT);
  pinMode(green_led, OUTPUT);
  pinMode(motor_1, OUTPUT);
  pinMode(motor_2, OUTPUT);

  analogWrite(lidar_speed, 210);

  check_battery();
  
  steering.attach(servo_pin);
  steering.write(zero_angle);
  Serial.println("Start");
  //debug.println("Start");
  attachInterrupt(digitalPinToInterrupt(enc_a), encoder, CHANGE);
  attachInterrupt(digitalPinToInterrupt(enc_b), encoder, CHANGE);
  attachInterrupt(digitalPinToInterrupt(enc_r_a), encoder_r, CHANGE);
  attachInterrupt(digitalPinToInterrupt(enc_r_b), encoder_r, CHANGE);
  attachInterrupt(digitalPinToInterrupt(enc_l_a), encoder_l, CHANGE);
  attachInterrupt(digitalPinToInterrupt(enc_l_b), encoder_l, CHANGE);
  attachInterrupt(start_btn, start_moving, FALLING);

  delay(1000);
}

void loop(){
  //debug_parse();
  calculate_speed();
  get_data_from_camera();
  /*debug.print(camera_blob_color);
  debug.print(" ");
  debug.print(camera_blob_side);
  debug.print(" ");
  debug.println(camera_blob_distance);*/
  LidarRead();
  controll_speed();
  //odometry();
}

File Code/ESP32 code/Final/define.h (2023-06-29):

#include <Arduino.h>
#include <Servo.h>
#include "BluetoothSerial.h"
#include <math.h>
#include <Wire.h>
#include "TrackingCamI2C.h"

#define enc_a 32
#define enc_b 33
#define motor_1 23
#define motor_2 19

#define enc_l_a 36
#define enc_l_b 15
#define enc_r_a 18
#define enc_r_b 39

#define servo_pin 14
#define servo_angle_pin 34

#define lidar_speed 13

#define green_led 2
#define red_led 12
#define start_btn 25
#define battery_voltage_pin 35


#define critical_voltage 7.5
#define devision_coefficient 416

#define zero_angle 87
#define angle_constrain 48
#define ideal_angle 41
#define iMin -50
#define iMax 50

#define min_mot_signal 30

#define line_calculation_angle 40

#define distance_to_wall 500
#define turn_radius 200//400//600
#define corner_entrance_distance 100//200
#define turn_time 450//550

#define is_corner_in_segment_value 500
#define blob_search_area 75
#define points_in_blob_area 2
#define distance_shift 20
#define robot_reached_point_distance 100

#define wheeel_base_width 88.5

#define pot_value 1650
#define values_per_angle 15.75



#ifndef DEFINE_H
#define DEFINE_H

#define SerialLidar Serial2
#define LIDAR_HEADER 0x54
#define LIDAR_LENGTH 0x2C
#define POINT_PER_PACK 12


struct point{
    int x;
    int y;

    point(int X=0, int Y=0)
    {
        x = X;
        y = Y;
    }

    void print(){
        Serial.print(this->x);
        Serial.print(':');
        Serial.print(this->y);
        Serial.print(' ');
    }

    void print_byte(){
        Serial.write(this->x);
        Serial.write(':');
        Serial.write(this->y);
        Serial.write(' ');
    }
};

struct point_d{
    double x;
    double y;
};

struct point_l{
    long long x;
    long long y;
};

struct point_raw{
    volatile unsigned int dist;
    volatile float angle;
    void print(){
        Serial.print(this->angle);
        Serial.print(':');
        Serial.print(this->dist);
        Serial.print(' ');
    }
};

struct lidar_data{
    point_raw points[400];
    volatile bool new_revolution = false;
    volatile float current_angle = 0;
    volatile int current_point = 0;
    volatile float last_angle = 0;
    volatile int points_amount = 0;
    volatile int pakets = 0;
};

extern Servo steering;
extern BluetoothSerial debug;
extern const int enc_table[16];
extern volatile long long int enc_count;
extern volatile long long int enc_count_last;
extern volatile long long int enc_count_l;
extern volatile long long int enc_count_r;
extern float speed_kP;
extern float speed_kI;
extern float speed_kD;
extern float speed_i_sum;
extern float last_error_speed;
extern float current_speed;
extern unsigned long long time_passed;
extern unsigned long long speed_calculation_timer;
extern int target_speed;
extern int distances[3];
extern int deviation_from_center;
extern float steering_kP;
extern float steering_kI;
extern float steering_kD;
extern float steering_i_sum;
extern float last_error_steering;
extern lidar_data lidar;
extern point points_xy[400];
extern int distance_to_forward_line;
extern int distance_to_back_line;
extern bool turning;
extern volatile bool reading_flag;
extern long bad_package_count;
extern long good_package_count;
extern bool move;
extern int turns_count;
extern int move_direction;
extern int16_t circle_buff[1500];
extern int circle_buff_pointer;
extern float angle_to_side_line;
extern int temporary_distance_to_wall;
extern int temporary_distance_to_wall2;
extern int distance_to_side_line;
extern point blobs_pot_coords[12];
extern float angle_to_forward_line;
extern point unfiltered_points[400];
extern bool print_flag;
extern unsigned short blobs_indexes[10];
extern unsigned short blobs_indexes_count;
extern bool orient_by;
extern int distance_to_side_line_for_PID;
extern int target_distance_to_wall;
extern unsigned short blob_detection_count[24];
extern int robot_x_local;
extern int robot_y_local;
extern float robot_angle_local;
extern int robot_x_global;
extern int robot_y_global;
extern int robot_sector;
extern short camera_blob_side;
extern short camera_blob_distance;
extern short camera_blob_color;
extern TrackingCamI2C trackingCam;

struct line{
    double a;
    double b;
    double c;

    void print(){
        Serial.print('{');
        Serial.print(this->a);
        Serial.print(':');
        Serial.print(this->b);
        Serial.print(':');
        Serial.print(this->c);
        Serial.print('}');
    }
};
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

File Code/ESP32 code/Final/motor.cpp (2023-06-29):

#include <define.h>

unsigned long long stuck_protection_timer = 0;
bool stuck_protection_flag = 0;
int signal_to_motor = 0;

bool go_flag=0;

unsigned long long controll_speed_timer = 0;

unsigned long long distance_traveled = 0;

float odometry_x = 0;
float odometry_y = 0;
float odomety_angle = 0;

unsigned long long odometry_calculation_timer = 0;

bool print_flag = 0;

unsigned long long enc_l_timer=0;
unsigned long long enc_l_last_time=0;

unsigned long long enc_count_global = 0;


void encoder(){
    static byte enc;
    enc = enc << 2;
    enc = enc | (digitalRead(enc_a) << 1 | digitalRead(enc_b));
    enc_count += enc_table[enc & 0b1111];
    enc_count_global += enc_table[enc & 0b1111];
}

void encoder_l(){
    static byte enc_l;
    enc_l = enc_l << 2;
    enc_l = enc_l | (digitalRead(enc_l_a) << 1 | digitalRead(enc_l_b));
    enc_count_l += enc_table[enc_l & 0b1111];
    enc_l_last_time = millis()-enc_l_timer;
    enc_l_timer = millis();
}

void encoder_r(){
    static byte enc_r;
    enc_r = enc_r << 2;
    enc_r = enc_r | (digitalRead(enc_r_a) << 1 | digitalRead(enc_r_b));
    enc_count_r += enc_table[enc_r & 0b1111];
    print_flag = 1;
}

void odometry(){
    if(millis() - odometry_calculation_timer > 100){
        odometry_calculation_timer = millis();

        Serial.print(enc_count_r);
        Serial.print(" ");
        Serial.print(enc_count_l);
        Serial.print(" : ");

        float enc_count_l_tmp = enc_count_l *= 1.93;
        //enc_count_l += 1.93*((millis()-enc_l_timer)/enc_l_last_time);
        float enc_count_r_tmp = enc_count_r *= 1.93;

        if (enc_count_l_tmp == enc_count_r_tmp) {
            odometry_y += enc_count_r_tmp;
        } 
        else {

            /*float angle_of_turn = (enc_count_r - enc_count_l) / wheeel_base_width;
            float distance = (enc_count_r + enc_count_l) / 2;
            odomety_angle += angle_of_turn;
            odometry_x += distance * cos(odomety_angle);
            odometry_y += distance * sin(odomety_angle);*/


            float angle_of_turn = (enc_count_r_tmp - enc_count_l_tmp) / wheeel_base_width;
            float distance = (enc_count_r_tmp + enc_count_l_tmp) / 2;
            float radius_of_turn = distance/angle_of_turn;
            float hyp = sqrt(2*pow(radius_of_turn, 2)*(1-cos(angle_of_turn)));
            odometry_x += hyp * cos(angle_of_turn/2);
            odometry_y += hyp * sin(angle_of_turn/2);
            odomety_angle += angle_of_turn;

            Serial.print(angle_of_turn);
            Serial.print(" ");
            Serial.print(distance);
            Serial.print(" ");
            Serial.print(radius_of_turn);
            Serial.print(" ");
            Serial.print(hyp);
            Serial.print(" : ");

        }

        
        Serial.print(odometry_x);
        Serial.print(" ");
        Serial.print(odometry_y);
        Serial.print(" ");
        Serial.println(((odomety_angle)/(2*PI))*360);

        enc_count_l = 0;
        enc_count_r = 0;
    }
}

void calculate_speed(){
    if(millis() - speed_calculation_timer >= 50){
        current_speed = -(float(enc_count)/(millis()-speed_calculation_timer));
        current_speed *= 5;
        speed_calculation_timer = millis();
        //odometry_2();
        enc_count = 0;
        //Serial.println(current_speed);
    }
    //stuck_protection();
}

void stuck_protection(){
    if(!stuck_protection_flag && current_speed == 0 && signal_to_motor>50){
        stuck_protection_flag = 1;
        stuck_protection_timer = millis();
    }

    if(stuck_protection_flag && current_speed <= 0.1 && signal_to_motor>50 && millis() - stuck_protection_timer > 500){
        analogWrite(motor_2, 0);
        //analogWrite(motor_2, 0);
        digitalWrite(red_led, HIGH);
        while (true){
            delay(10);
        }
    }
    else if(stuck_protection_flag && millis() - stuck_protection_timer > 500){
        stuck_protection_timer = millis();
        stuck_protection_flag = 0;
    }
}

void odometry_2(){
    float real_servo_angle = (analogRead(servo_angle_pin)-pot_value)/values_per_angle;
    Serial.print(real_servo_angle);
    Serial.print(" ");
    Serial.println(enc_count);
}

void start_moving(){
    if(!go_flag){
        move = true;
        //digitalWrite(green_led, 90);
        target_speed = 17;
        speed_kP = 1;
        Serial.println("Go");
        //Serial.print(temporary_distance_to_wall);Serial.print(" ");Serial.println(temporary_distance_to_wall2);
        go_flag=1;
    }
}

float speed_pid(int error){
    //ПИД для контроля скорости мотора

    float up = error * speed_kP;
    speed_i_sum += error;
    float ui = speed_i_sum * speed_kI;
    if (ui < iMin){
        ui = iMin;
    }
    if (ui > iMax){
        ui = iMax;
    }
    float ud = (error - last_error_speed) * speed_kD;
    last_error_speed = error;
    float output = up + ui + ud;
    return output;
}

void controll_speed(){
    //Функция 

    if (millis() - controll_speed_timer > 50){
        controll_speed_timer = millis();

        signal_to_motor = int(speed_pid(target_speed-int(current_speed+0.5)) + /*1.8*/2.5*(target_speed) + 0.5);

        if (signal_to_motor > 255){
            signal_to_motor = 255;
        }
        if (signal_to_motor < 0){
            signal_to_motor = 0;
        }
        if (signal_to_motor < min_mot_signal){
            signal_to_motor = 0;
        }

        //Serial.print(target_speed);Serial.print(" ");Serial.print(current_speed);Serial.print(" ");Serial.println(signal_to_motor);
        if(signal_to_motor == 0){
            //digitalWrite(motor_1, LOW);
            analogWrite(motor_2, 0);
        }
        else{
            //digitalWrite(motor_1, HIGH);
            analogWrite(motor_2, signal_to_motor);
        }
    }
}

void set_speed(int target_speed){
    if (target_speed > 255){
        target_speed = 255;
    }
    if (target_speed < min_mot_signal && target_speed > 0){
        target_speed = 0;
    }
    signal_to_motor = target_speed;
    if (target_speed <= 0){
        //digitalWrite(motor_1, LOW);
        analogWrite(motor_2, 0);
    }
    else{
        //digitalWrite(motor_1, HIGH);
        analogWrite(motor_2, target_speed);
    }
    
}

void set_steer_angle(float angle){
    if (angle > angle_constrain){
        angle = angle_constrain;
    }
    if (angle < -angle_constrain){
        angle = -angle_constrain;
    }
    float real_angle = zero_angle + angle;
    steering.write(real_angle);
}

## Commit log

2023-06-29 Models Update
    [WRO v25.step, WRO v26.step, Защита камеры.stl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]
2023-06-29 Schematic diagram update
2023-06-29 Schematic diagram uptdate
